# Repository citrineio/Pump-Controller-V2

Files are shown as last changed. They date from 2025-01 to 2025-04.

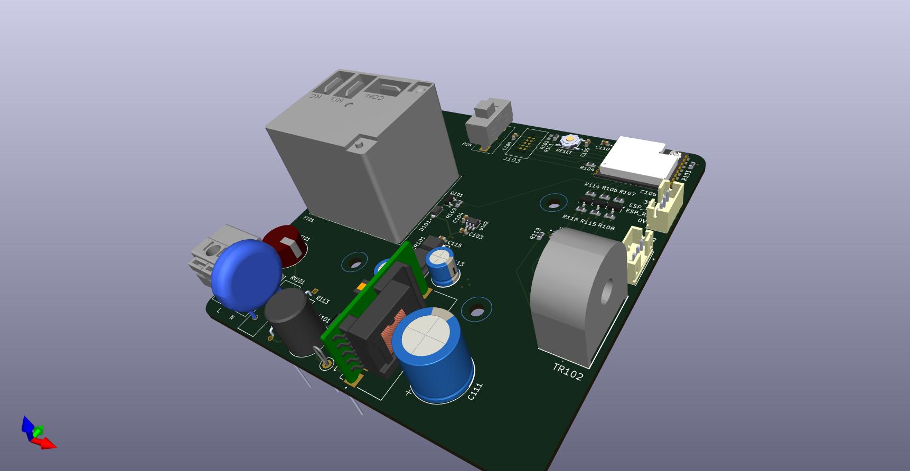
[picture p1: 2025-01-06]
01- Design Files/V4.0/Pump_Controller Side.jpg

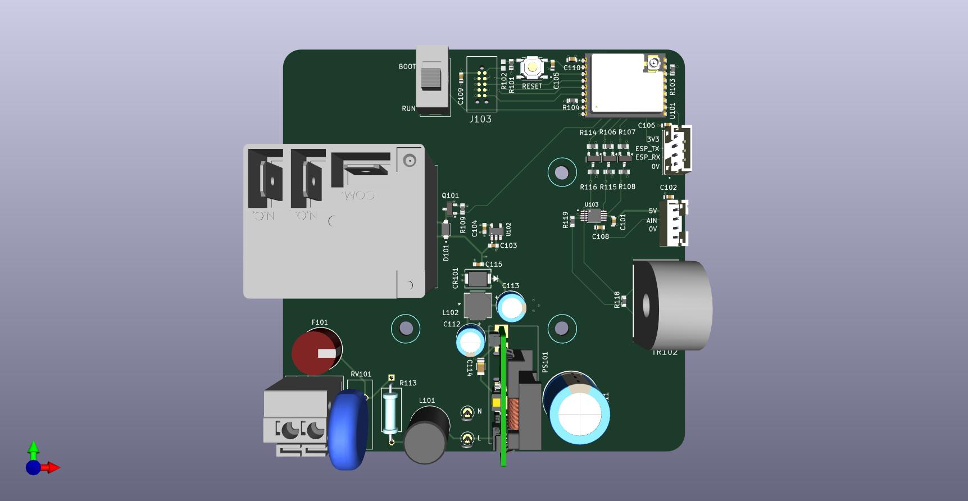
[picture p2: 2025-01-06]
01- Design Files/V4.0/Pump_Controller.jpg

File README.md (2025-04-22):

# Pump Controller

## Description
A device which can monitor and switch household water pumps remotely.
## Constraints
**Power**:  5V wall power adaptor
## Features
- Monitor the on/off status and current consumption
- Switch the pump off if desired.
- Indicate if the pump is running dry. 
- Wireless connectivity
- Matter optional

## Block Diagram

Pump Controller V2

## PCB





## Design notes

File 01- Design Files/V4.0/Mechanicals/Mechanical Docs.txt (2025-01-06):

- Board Outline dxf
- Enclosure STEP File

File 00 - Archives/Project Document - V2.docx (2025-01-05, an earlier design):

# Project Title

# Description

A device which can monitor and switch household water pumps remotely.

# Constraints

Power: Mains voltage 100-240V

Dimensions: Must fit within a typical junction box, preferably a 10x10cm box

# Features

- Monitor the On/Off status and current consumption
- Switch the pump off if desired.
- Indicate if the pump is running dry.
- Wireless connectivity
- Matter optional

# Block Diagram

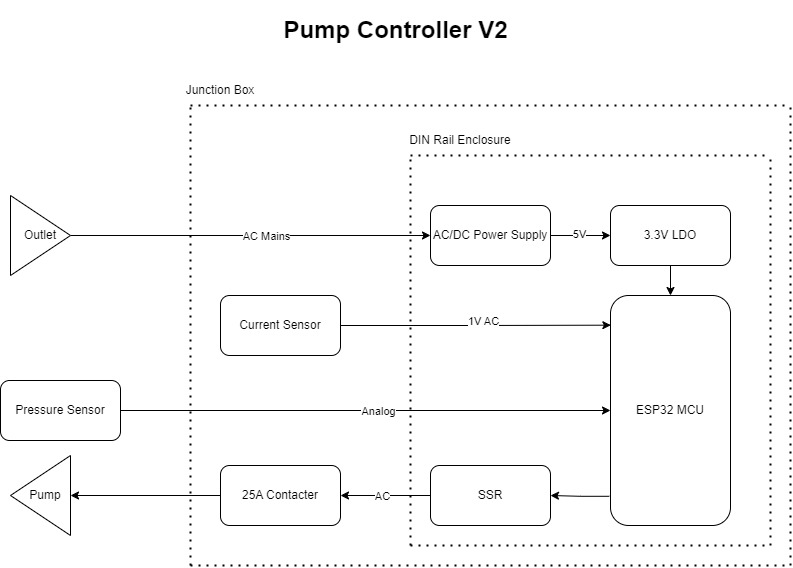
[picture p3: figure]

# Components

MCU: ESP32-C3-MINI-1U-H4

## AC/DC Power Supply: IRM-03-5

## 3.3V LDO: AP2112K-3.3TRG1

## Current Sensor: SCT013-30

Pressure Sensor: Seeed 114991178 or equivalent.

SSR: AQH2223AX

Contactor: Tomzn TOCT1-25 (Aliexpress)

Din Rail Enclosure: Szomk AK-DR-103, LK SHINY LK-DR56 or BUD IND DMB-4771

Box: Minimum 12x12cm

# Power Budget

Component | Voltage/s | Current/s | Power | Type
IRM-03-5 | 5V | 0.6A | 3W | Source
AP2112K-3.3TRG1 | 3.3V | 0.6A | 1.98 | Source
ESP32-C3-MINI-1U-H4 | 3.3V | 0.35A | 1.15W | Sink
114991178 | 5 | 0.01 | 0.05W | Sink
AQH2223AX | 5 | 0.02 | 0.1W | Sink
Total | 1.3W

*Some ICs have multiple voltage rails with different voltage levels.

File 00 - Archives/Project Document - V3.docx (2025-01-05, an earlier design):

# Pump Controller

# Description

A device which can monitor and switch household water pumps remotely.

This version forgoes din rail mounted components including the PCB enclosure and the contactor in favor of a chassis mounted heavy contact relay and a standoff mounted PCB. It also switches to an open frame AC/DC module decreasing the price.

# Constraints

Power: Mains voltage 100-240V

Dimensions: Must fit within a typical junction box, preferably a 10x10cm box

# Features

- Monitor the on/off status and current consumption
- Switch the pump off if desired.
- Indicate if the pump is running dry.
- Wireless connectivity
- Matter optional

# Block Diagram

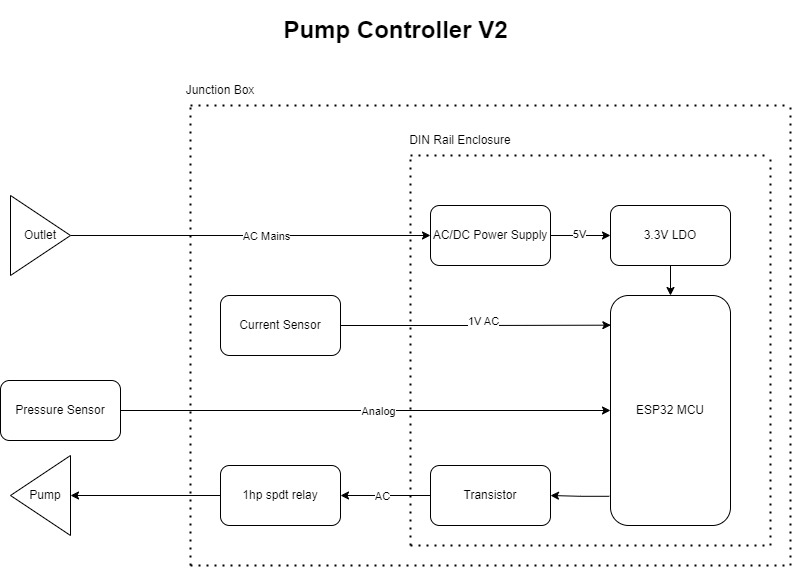
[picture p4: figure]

# Future Improvements

- Utilize 3.81mm or 5.08mm plug-in terminal blocks instead of spring clamp blocks for AC power.
- Utilize 3.81mm plug-in terminal blocks instead of JST connectors.
- Avoid 2.0mm connectors in the future and stick with 2.54mm to enable Dupont cables.
- Replace TC2050 with custom 2x5 2.54mm ISP footprint to utilize testing clamp.
- Replace UART connector with 1x4 2.54mm connector footprint for testing clamp.
- Use Hi-link HLK-PM01 for this application.
- Design a custom enclosure for the PCB and redesign the whole PCB.

# Components

MCU: ESP32-C3-WROOM-02U-N4

## AC/DC Power Supply: PBO-5C-5 2.8$ OR LS05-13B05R3 OR 5ACFEW_05S3

Fuse Holder: 56000001019 or 56000001009

Fuse: 39212000000 or 0034.6618

MOV: B72214S0351K101

Resistor: FMP200JR-52-12R

Input Inductor: RLB9012-472KL

Capacitor: B43821F5226M000

CY: CL31B102KHFNFNE

Output Cap: A750EQ477M1CAAE015

Output inductor: LSXBD6060WHL4R7M

Output Cap 2: ESL107M035AE3AA

TVS: SMBJ7.0CA-13-F

CAP 3: CL10B105KO8NNNC

## 3.3V LDO: AP2112K-3.3TRG1

Zmct102 (pcb mount)

Terminals: WJ142V-5.08-2P

JST Connector: B3B-XH-2(LF)(SN)

Pressure Sensor: Seeed 114991178 or equivalent.

Terminal Block: XY118-5.0-2P

ADC?

Relay: J115F21C5VDCS_9 or az2100-1ce-5def or SLC-5VDC-SL-C

Flyback Diode: 1N4007FL

Transistor: DMG2302U-7

Box: 10x10cm CCTV box

# Power Budget

Component | Voltage/s | Current/s | Power | Type
PBO-5C-5 | 5V | 1A | 5W | Source
AP2112K-3.3TRG1 | 3.3V | 0.6A | 1.98 | Source
ESP32-C3-WROOM-02U-N4 | 3.3V | 0.35A | 1.15W | Sink
114991178 | 5 | 0.01 | 0.05W | Sink
J115F31CH5VDCS61.5U | 5 | 0.3 | 1.5W | Sink
Total | 1.3W

*Some ICs have multiple voltage rails with different voltage levels.

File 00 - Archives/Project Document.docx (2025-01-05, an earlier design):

# Project Title

# Description

A device/product which does X and Y or solves problem Z

# Constraints

Power: Particular power source/ specific battery life

Dimensions: Must fit a specific enclosure

Input/Output Interface:

Specific Components

*These are examples.

# Features

- Can do X
- Connects to Y
- Control Z
- Senses A

# Block Diagram

Having a block diagram is imperative for a quick design process. DRAW.IO is a decent tool.

# Components

MCU/MPU/FPGA/ASIC: Part number of the main IC

Criteria | IC 1 | IC 2
Price | $ | $
Package | QFP/QFN/BGA/SOIC…etc
Manufacturer
Current | Max current consumption/rating
Input Voltage | Min – Max voltage/ nominal voltage
| Mark selected component in green

## Component 1

# Power Budget

Component | Voltage/s | Current/s | Power
Part number 1 | Voltage 1, Voltage 2, Voltage 3… | Current 1, Current 2, Current 3… | Total Power
Part number 2 | Input Voltage | Current Consumption | Power
Part number 3 | Input Voltage | Current Consumption | Power
Total | Total power in Watts

*Some ICs have multiple voltage rails with different voltage levels.

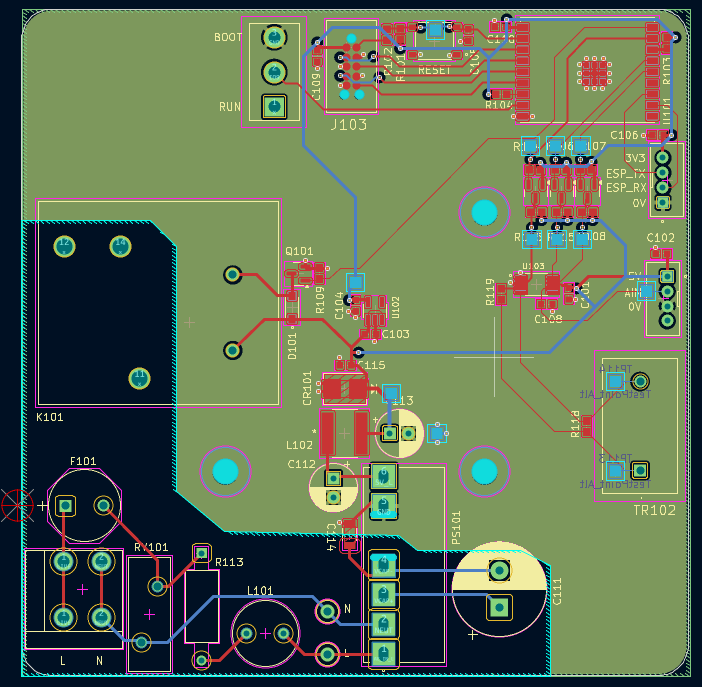
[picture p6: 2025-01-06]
01- Design Files/V4.0/Layout .png

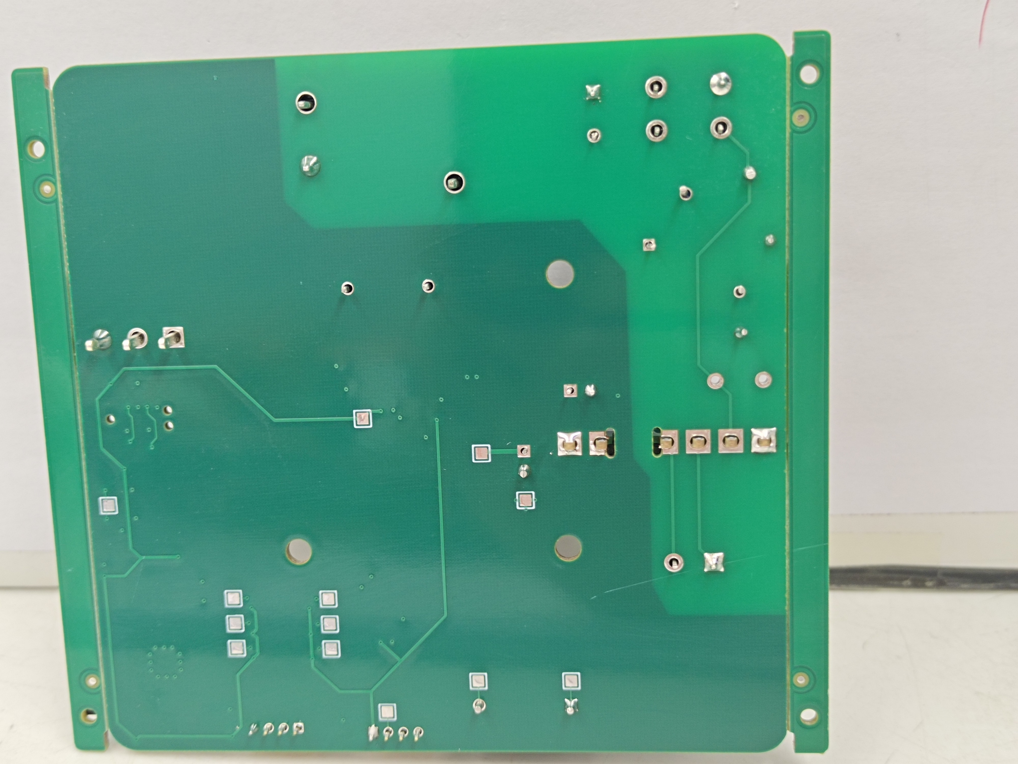
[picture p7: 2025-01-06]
02 - Photos/wKgZomYt3oqAXZ4lACKfuGCoQko008.jpg

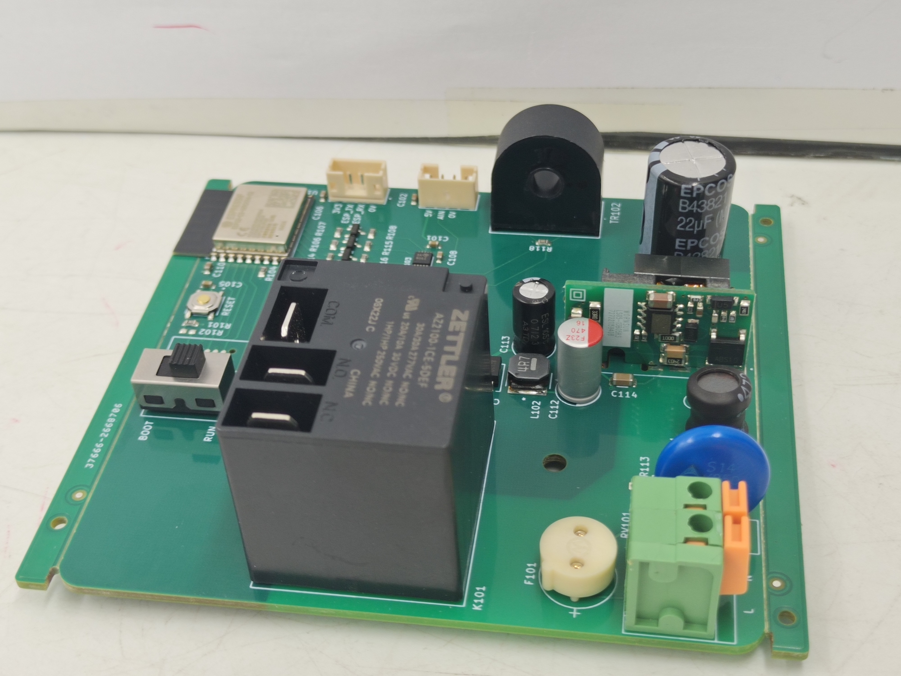
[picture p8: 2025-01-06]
02 - Photos/wKgaomYt3ouAErzlABsgimlviy8659.jpg

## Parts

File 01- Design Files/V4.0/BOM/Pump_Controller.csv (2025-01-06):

Reference | Value | Footprint | Qty | DNP | Manufacturer | Part Number
C101,C102,C103,C104,C106,C108,C109,C110,C111,C112,C113 | 1u | Library:CL10A | 11 |  | Samsung Electro-Mechanics | CL10B105KO8NNNC
C105,C107 | 10u | UltraLibrarian:CAP_CL21_SAM | 2 |  | Samsung Electro-Mechanics | CL21A106KAYNNNE
D101,D103 | 1N5819HW-7-F | Diode_SMD:D_SOD-123 | 2 |  | Diodes Incorporated | 1N5819HW-7-F
D102 | GRN | LED_SMD:LED_0603_1608Metric | 1 |  | Everlight Elec | 19-217/GHC-YR1S2/3T
F101 | SRF1206P150 | Library:PTC_1206_3216Metric | 1 |  | prosemi | SRF1206P150
J101,J106,J107 | Screw_Terminal_01x02 | Samacsys:DG30825402P1400AH | 3 |  | DEGSON | DG308-2.54-02P-14-00A(H)
J102 | Conn_01x04 | Connector_PinHeader_2.54mm:PinHeader_1x04_P2.54mm_Vertical | 1
J104 | Conn_02x05_Odd_Even | Connector_PinHeader_2.54mm:PinHeader_2x05_P2.54mm_Vertical | 1
J105 | Screw_Terminal_01x03 | Samacsys:DG30825403P1400AH | 1 |  | DEGSON | DG308-2.54-03P-14-00A(H)
K101 | AZ2100-1CE-5DEF | Library:AZ2100-1CE-5DEF | 1 |  | American Zettler | AZ2100-1CE-5DEF
Q101,Q103 | C20917 | Package_TO_SOT_SMD:SOT-23 | 2 |  | Alpha & Omega Semicon | AO3400A
R101,R102,R103,R107,R108,R110,R111,R115 | 10K | Library:RESC1607X60N | 8 |  | UNI-ROYAL(Uniroyal Elec) | 0603WAF1002T5E
R104,R105,R113 | 2k2 | Library:RESC1607X60N | 3 |  | UNI-ROYAL(Uniroyal Elec) | 0603WAF2201T5E
R109 | 68R | Library:RESC1607X60N | 1 |  | UNI-ROYAL(Uniroyal Elec) | 0603WAF680JT5E
TR101 | ZMCT102 | Library:zmct102 | 1 |  | Qingxian Zeming Langxi Electronic | ZMCT102
U101 | AP2112K-3.3 | Library:SOT95P285X140-5N | 1 |  | Diodes Incorporated | AP2112K-3.3TRG1
U102 | ESP32-C3-WROOM | Library:MODULE_ESP32-C3-WROOM-02-H4 | 1 |  | Espressif Systems | ESP32-C3-WROOM-02-N4
U103 | TXS0104EPWR | Snapeda:TXS0104EPWR_SOP65P640X120-14N | 1
U104 | ADS1115IDGSR | Library:ADS1115_SOP50P490X110-10N | 1 |  | Texas Instruments | ADS1115IDGSR

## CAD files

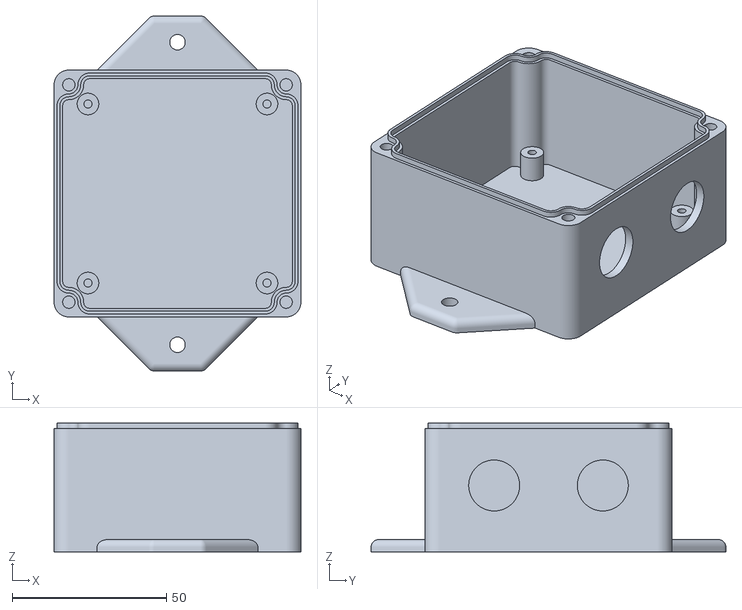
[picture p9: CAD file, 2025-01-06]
01- Design Files/V4.0/Mechanicals/Enclosure/C-1Y6W328612A_box_V6.1.stl
80.0 x 115.0 x 41.7

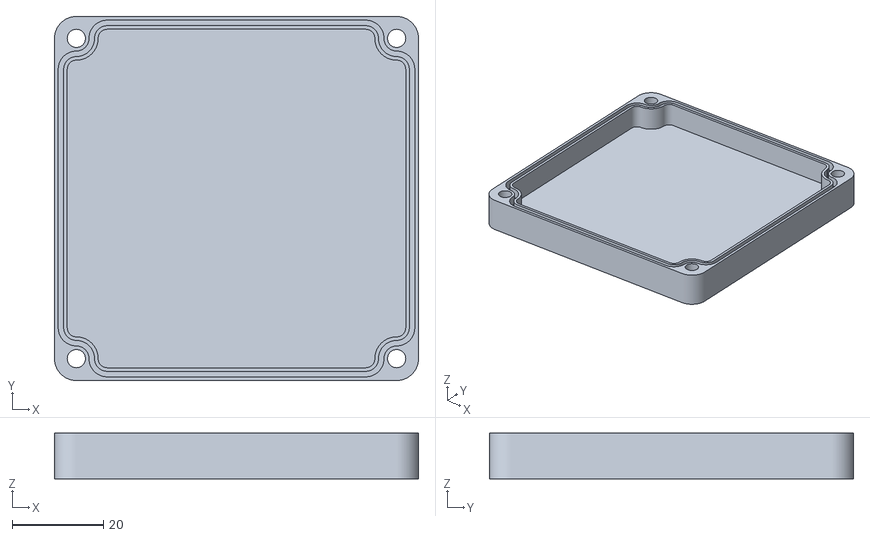
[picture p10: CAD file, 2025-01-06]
01- Design Files/V4.0/Mechanicals/Enclosure/C-1Y5W328612A_lid.stl
80.0 x 80.0 x 10.00

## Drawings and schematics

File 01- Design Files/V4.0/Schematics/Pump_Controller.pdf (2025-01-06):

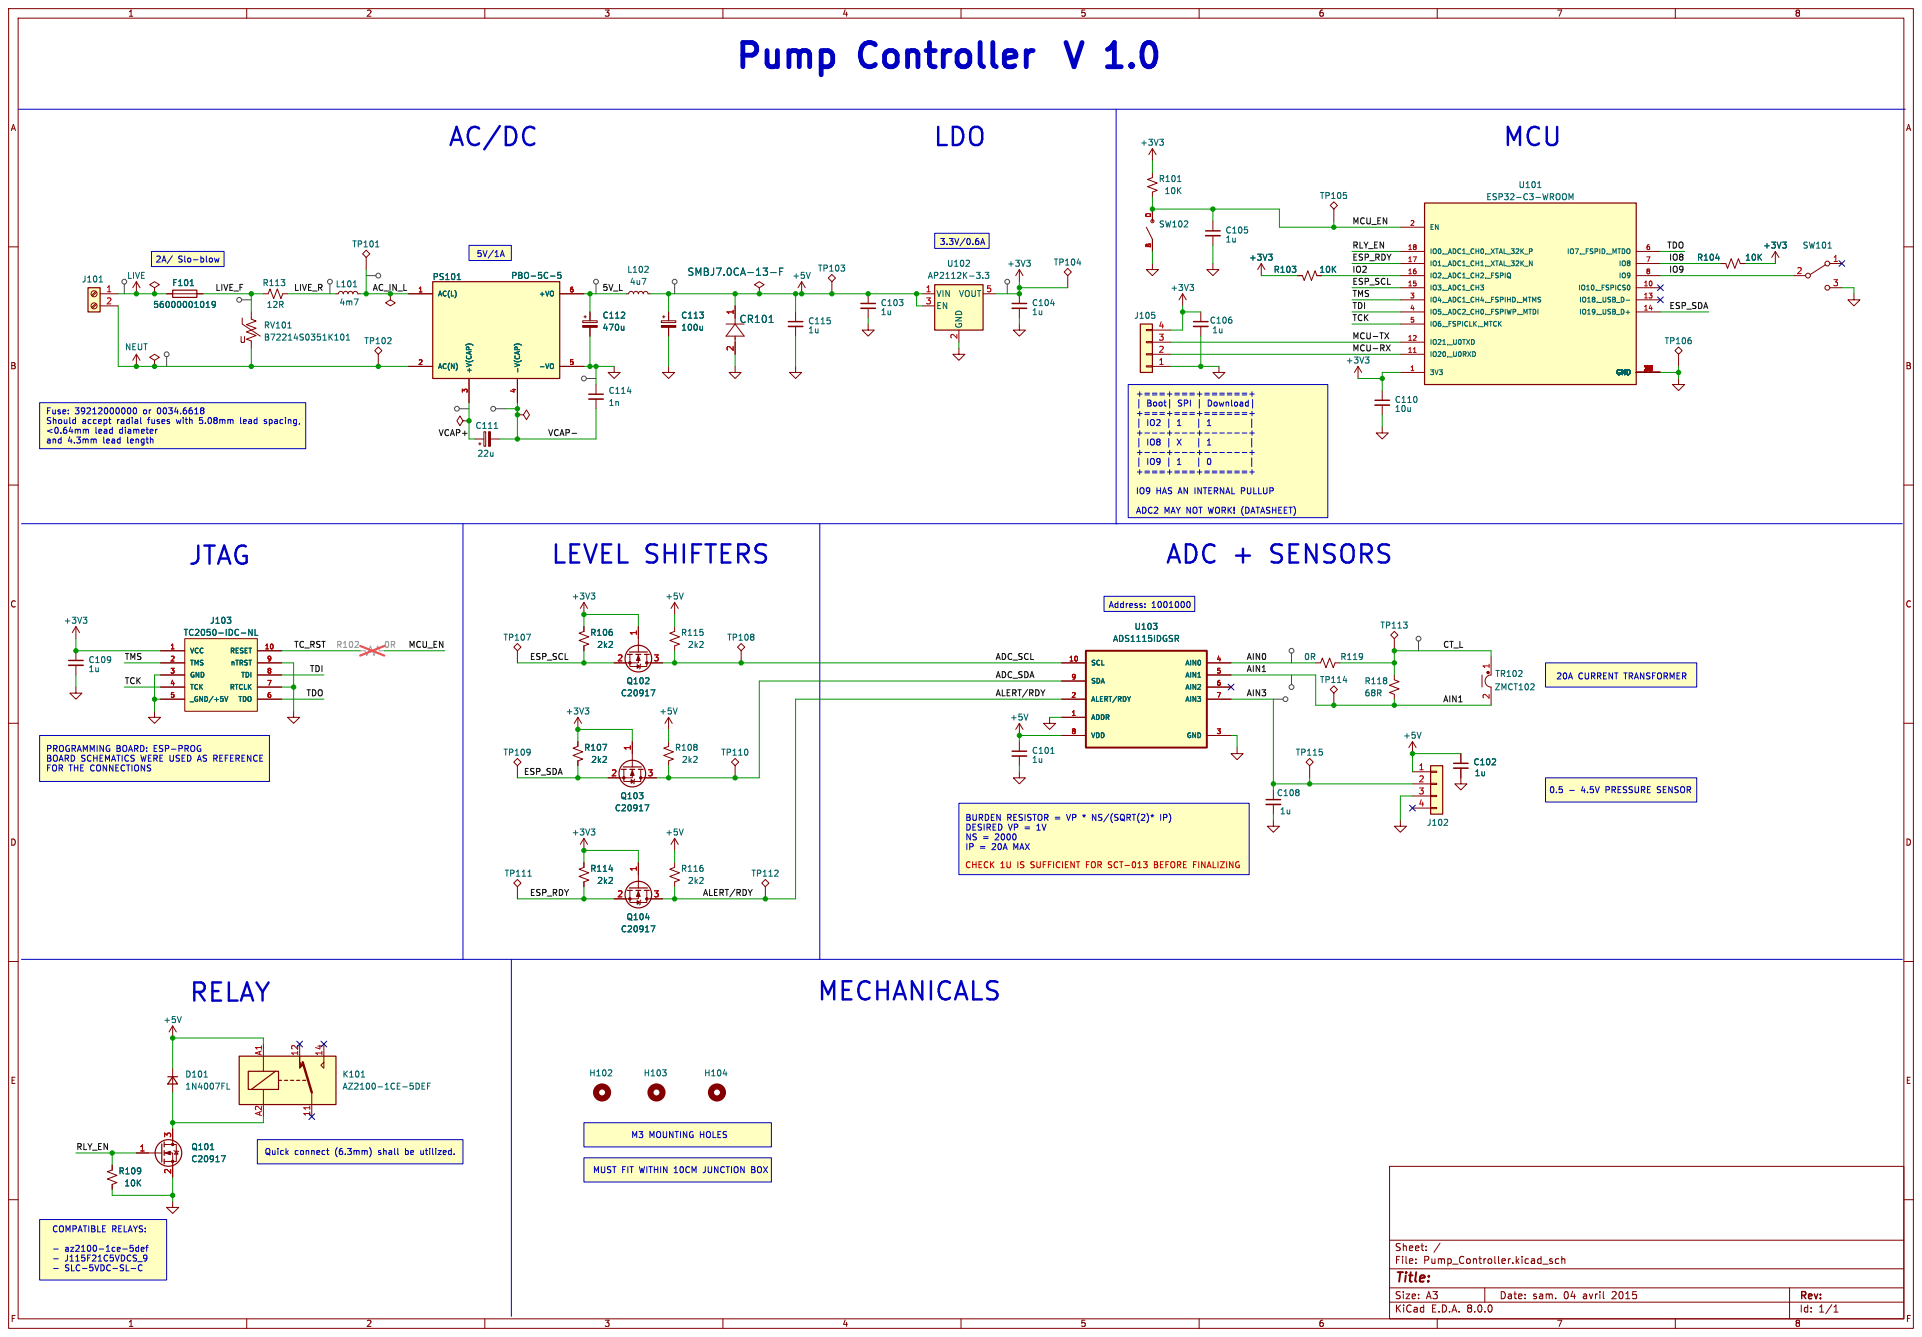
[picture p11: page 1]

IP = 20A MAX Pump Controller

IO9 HAS AN INTERNAL PULLUP
ADC + SENSORS

ADC2 MAY NOT WORK! (DATASHEET) M3 MOUNTING HOLES

PROGRAMMING BOARD: ESP-PROG
BOARD SCHEMATICS WERE USED AS REFERENCE

MUST FIT WITHIN 10CM JUNCTION BOX

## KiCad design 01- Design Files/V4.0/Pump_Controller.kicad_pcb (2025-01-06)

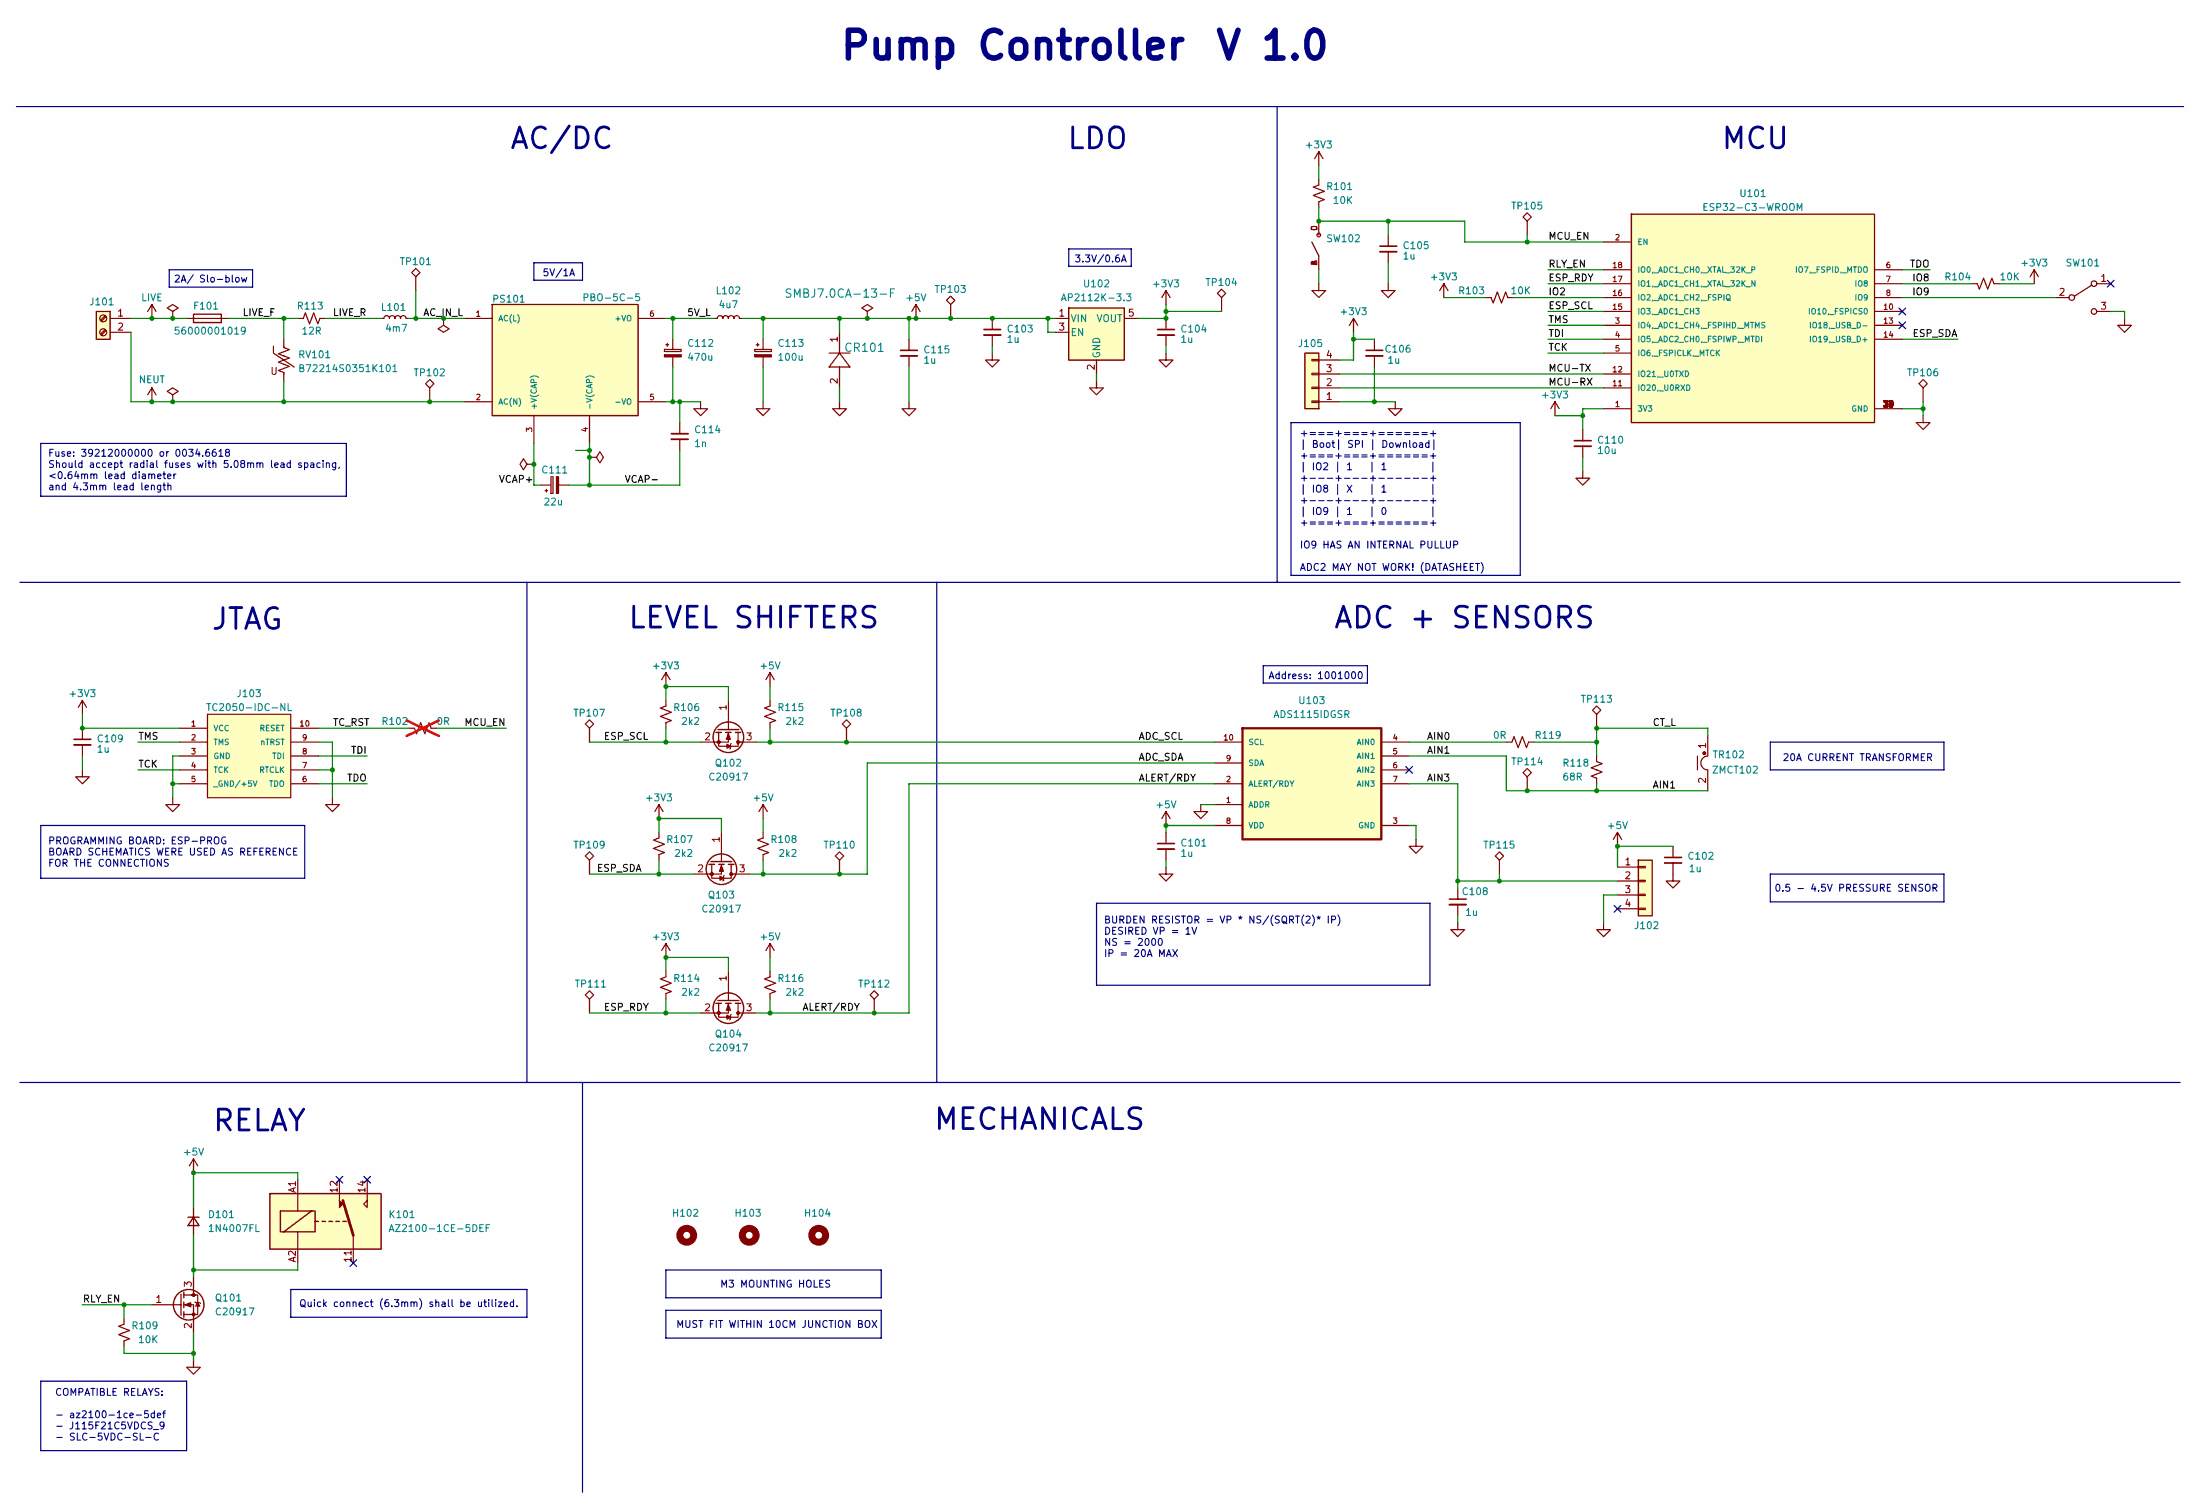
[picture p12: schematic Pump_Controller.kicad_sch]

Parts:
C101, C102, C103, C104, C105, C106, C108, C109, C115: 1u; CL10A; Part Number CL10B105KO8NNNC - C59782
C110: 10u; CL10A; Part Number CL10A106MA8NRNC - C96446
C111: 22u; CP_Radial_D12.5mm_P5.00mm; Part Number B43821F5226M000
C112: 470u; CP_Radial_D6.3mm_P2.50mm; Part Number A750EQ477M1CAAE015
C113: 100u; CP_Radial_D6.3mm_P2.50mm; Part Number ESL107M035AE3AA
C114: 1n; CAP_CL31_SAM; Part Number CL31B102KHFNFNE
CR101: SMBJ7.0CA-13-F; SMB_DIO; Part Number SMBJ7.0CA-13-F
D101: 1N4007FL; SODFL3618X110N; Part Number 1N4007FL
F101: 56000001019; FUSE_560_1019_LTF; Part Number 56000001019
H102, H103, H104: MountingHole; MountingHole_3.2mm_M3
J101: Screw_Terminal_01x02; CONN-TH_2P-P5.08_WJ142V-5.08-2P
J102, J105: B4B-PH-K; JST_B4B-PH-K; Part Number B4B-PH-K
J103: TC2050-IDC-NL; TAG-CONNECT_TC2050-IDC-NL
K101: AZ2100-1CE-5DEF; Part Number AZ2100-1CE-5DEF
L101: 4m7; IND_RLB9012-472KL; Part Number RLB9012-472KL
L102: 4u7; IND_HL4R7M_TAY; Part Number LSXBD6060WHL4R7M
PS101: PBO-5C-5; CONV_PBO-5C-5; Part Number PBO-5C-5
Q101, Q102, Q103, Q104: C20917; SOT-23; Part Number AO3400A
R101, R103, R104, R109: 10K; RESC1607X60N; Part Number 0603WAF1002T5E - C25804
R102: 0R; RESC1607X60N; Part Number 0603WAF0000T5E - C21189; not fitted
R106, R107, R108, R114, R115, R116: 2k2; RESC1607X60N; Part Number 0603WAF2201T5E- C4190
R113: 12R; YAG_FMP200_YAG; Part Number FMP200JR-52-12R
R118: 68R; RESC1607X60N; Part Number 0603WAF680JT5E- C27592
R119: 0R; RESC1607X60N; Part Number 0603WAF0000T5E - C21189
RV101: B72214S0351K101; VAR_B72214S0351K101; Part Number B72214S0351K101
SW101: SW_SPDT; SS12D10L3; Part Number SS-12D10L3
SW102: TS-1187A-B-A-B; SW_TS-1187A-B-A-B; Part Number TS-1187A-B-A-B
TP101, TP102: TestPoint_Alt; TestPoint_Loop_D2.50mm_Drill1.0mm
TP103, TP104, TP105, TP106, TP107, TP108, TP109, TP110, TP111, TP112, TP113, TP114, TP115: TestPoint_Alt; TestPoint_Pad_1.5x1.5mm
TR102: ZMCT102; zmct102; Part Number ZMCT102
U101: ESP32-C3-WROOM; XCVR_ESP32-C3-WROOM-02U-N4; Part Number ESP32-C3-WROOM-02-N4
U102: AP2112K-3.3; SOT95P285X140-5N; Part Number AP2112K-3.3
U103: ADS1115IDGSR; ADS1115_SOP50P490X110-10N; Part Number ADS1115IDGSR

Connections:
+3V3: C104.1, C106.1, C109.1, C110.1, J103.1 (VCC), J105.4, Q102.1 (G), Q103.1 (G), Q104.1 (G), R101.1, R103.1, R104.2, R106.1, R107.1, R114.1, TP104.1, U101.1 (3V3), U102.5 (VOUT)
+5V: C101.1, C102.1, C103.1, C113.1, C115.1, CR101.1, D101.1 (K), J102.1, K101.A1, L102.2, R108.1, R115.1, R116.1, TP103.1, U102.1 (VIN), U102.3 (EN), U103.8 (VDD)
/5V_L: C112.1, L102.1, PS101.6 (+VO)
/AC_IN_L: L101.2, PS101.1 (AC(L)), TP101.1
/ADC_SCL: Q102.3 (D), R115.2, TP108.1, U103.10 (SCL)
/ADC_SDA: Q103.3 (D), R108.2, TP110.1, U103.9 (SDA)
/AIN0: R119.2, U103.4 (AIN0)
/AIN1: R118.2, TP114.1, TR102.2, U103.5 (AIN1)
/AIN3: C108.1, J102.2, TP115.1, U103.7 (AIN3)
/ALERT/RDY: Q104.3 (D), R116.2, TP112.1, U103.2 (ALERT/RDY)
/CT_L: R118.1, R119.1, TP113.1, TR102.1
/ESP_RDY: Q104.2 (S), R114.2, TP111.1, U101.17 (IO1,_ADC1_CH1,_XTAL_32K_N)
/ESP_SCL: Q102.2 (S), R106.2, TP107.1, U101.15 (IO3,_ADC1_CH3)
/ESP_SDA: Q103.2 (S), R107.2, TP109.1, U101.14 (IO19,_USB_D+)
/IO2: R103.2, U101.16 (IO2,_ADC1_CH2,_FSPIQ)
/IO8: R104.1, U101.7 (IO8)
/IO9: SW101.2 (B), U101.8 (IO9)
/LIVE_F: F101.2, R113.1, RV101.1
/LIVE_R: L101.1, R113.2
/MCU-RX: J105.2, U101.11 (IO20,_U0RXD)
/MCU-TX: J105.3, U101.12 (IO21,_U0TXD)
/MCU_EN: C105.1, R101.2, R102.2, SW102.C, SW102.D, TP105.1, U101.2 (EN)
/RLY_EN: Q101.1 (G), R109.1, U101.18 (IO0,_ADC1_CH0,_XTAL_32K_P)
/TCK: J103.4 (TCK), U101.5 (IO6,_FSPICLK,_MTCK)
/TC_RST: J103.10 (RESET), R102.1
/TDI: J103.8 (TDI), U101.4 (IO5,_ADC2_CH0,_FSPIWP,_MTDI)
/TDO: J103.6 (TDO), U101.6 (IO7,_FSPID,_MTDO)
/TMS: J103.2 (TMS), U101.3 (IO4,_ADC1_CH4,_FSPIHD,_MTMS)
/VCAP+: C111.1, PS101.3 (+V(CAP))
/VCAP-: C111.2, C114.2, PS101.4 (-V(CAP))
GND: C101.2, C102.2, C103.2, C104.2, C105.2, C106.2, C108.2, C109.2, C110.2, C112.2, C113.2, C114.1, C115.2, CR101.2, J102.3, J103.3 (GND), J103.5 (_GND/+5V), J103.7 (RTCLK), J103.9 (nTRST), J105.1, PS101.5 (-VO), Q101.2 (S), R109.2, SW101.3 (C), SW102.A, SW102.B, TP106.1, U101.9 (GND), U101.19 (GND), U101.20 (GND), U101.21 (GND), U101.22 (GND), U101.23 (GND), U101.24 (GND), U101.25 (GND), U101.26 (GND), U101.27 (GND), U101.28 (GND), U101.29 (GND), U101.30 (GND), U101.31 (GND), U101.32 (GND), U101.33 (GND), U101.34 (GND), U101.35 (GND), U101.36 (GND), U101.37 (GND), U101.38 (GND), U101.39 (GND), U102.2 (GND), U103.1 (ADDR), U103.3 (GND)
LIVE: F101.1, J101.1
NEUT: J101.2, PS101.2 (AC(N)), RV101.2, TP102.1
unnamed: D101.2 (A), K101.A2, Q101.3 (D)

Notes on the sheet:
+===+===+======+ | Boot| SPI | Download| +===+===+======+ | IO2 | 1 | 1 | +---+---+------+ | IO8 | X | 1 | +---+---+------+ | IO9 | 1 | 0 | +===+===+======+ IO9 HAS AN INTERNAL PULLUP ADC2 MAY NOT WORK! (DATASHEET)
5V/1A
0.5 - 4.5V PRESSURE SENSOR
LEVEL SHIFTERS
Quick connect (6.3mm) shall be utilized.
3.3V/0.6A
AC/DC
MUST FIT WITHIN 10CM JUNCTION BOX
RELAY
COMPATIBLE RELAYS: - az2100-1ce-5def - J115F21C5VDCS_9 - SLC-5VDC-SL-C
BURDEN RESISTOR = VP * NS/(SQRT(2)* IP) DESIRED VP = 1V NS = 2000 IP = 20A MAX
PROGRAMMING BOARD: ESP-PROG BOARD SCHEMATICS WERE USED AS REFERENCE FOR THE CONNECTIONS
JTAG
M3 MOUNTING HOLES
20A CURRENT TRANSFORMER
Pump Controller
LDO
Fuse: 39212000000 or 0034.6618 Should accept radial fuses with 5.08mm lead spacing, <0.64mm lead diameter and 4.3mm lead length
Address: 1001000
MECHANICALS
2A/ Slo-blow
MCU
ADC + SENSORS
V 1.0

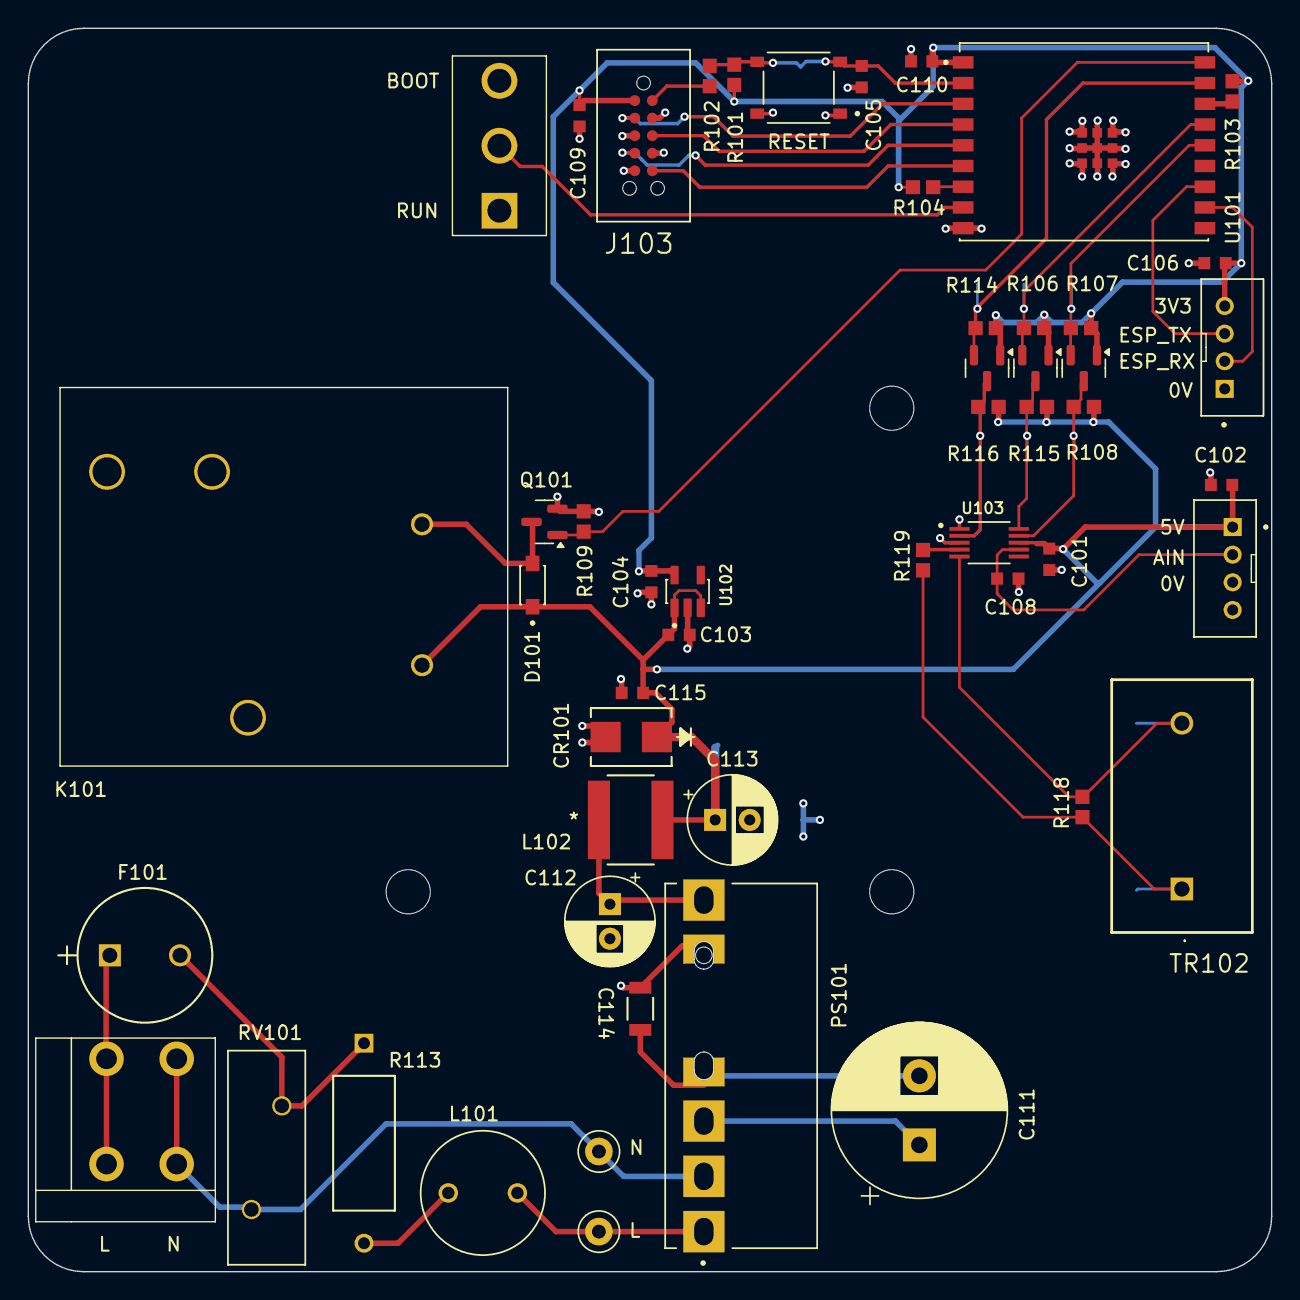
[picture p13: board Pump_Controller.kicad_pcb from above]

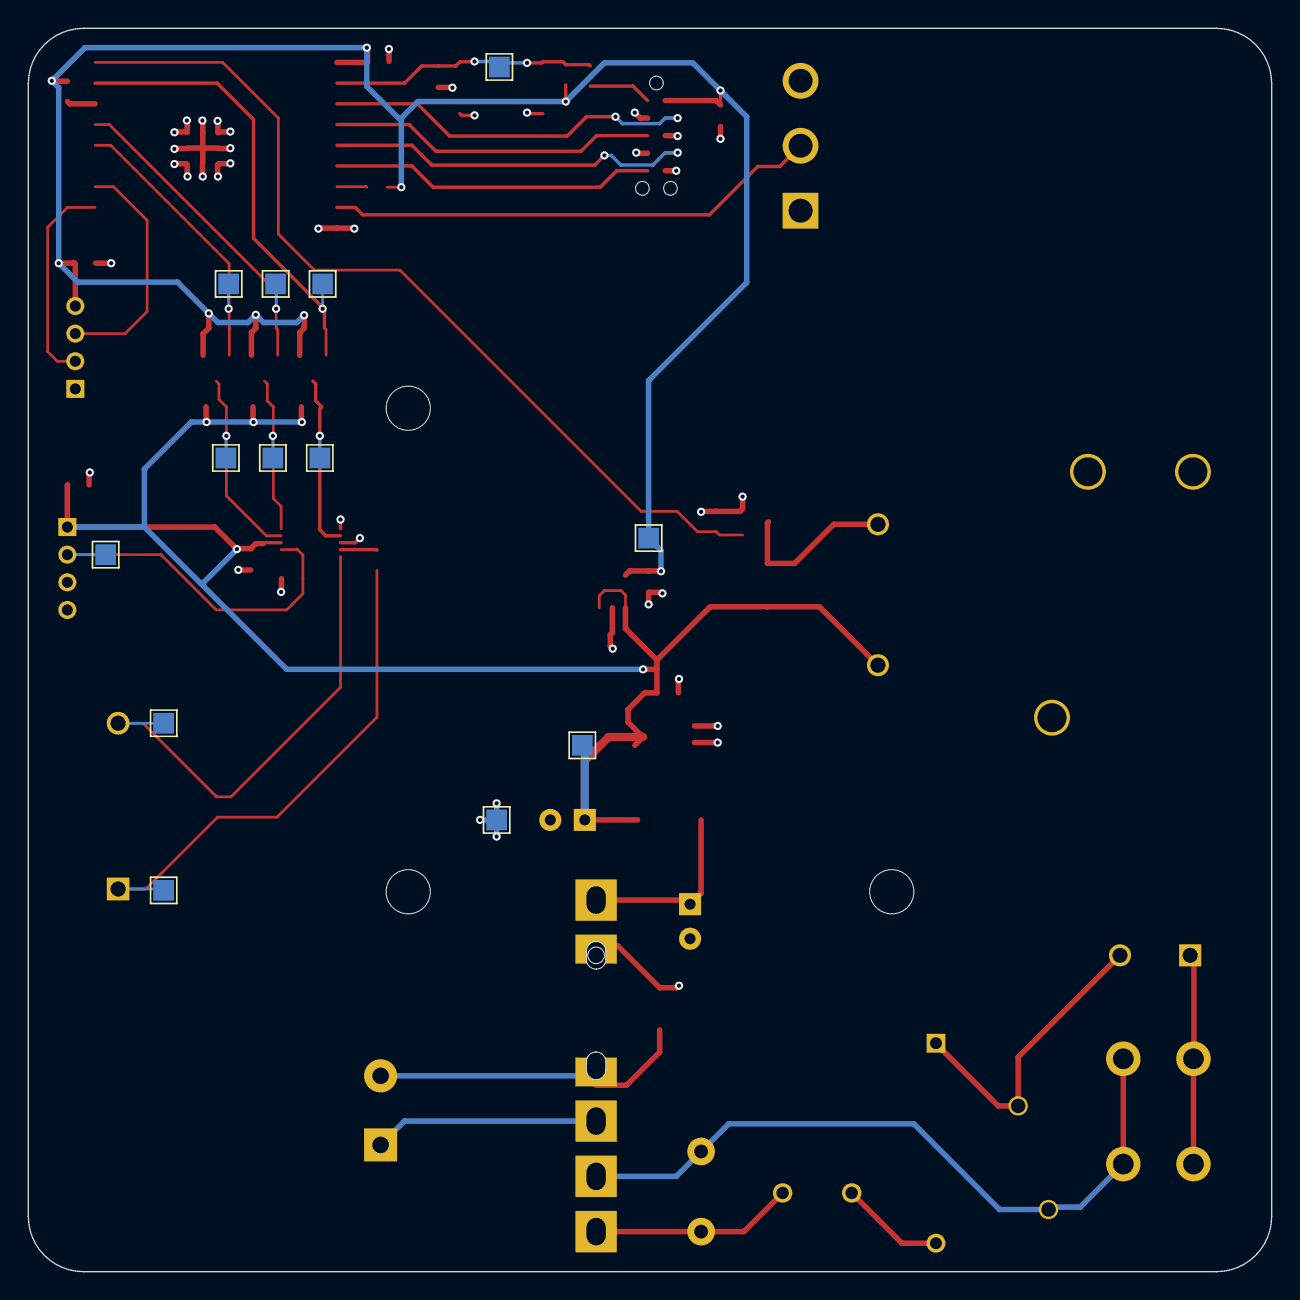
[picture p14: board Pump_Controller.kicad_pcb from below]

Board: 4 copper layers, 90.0 x 90.0 mm, 68 parts (13 on the bottom side), 34 nets.

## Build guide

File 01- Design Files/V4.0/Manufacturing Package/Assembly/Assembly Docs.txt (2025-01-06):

- Component Positions File (Pick and Place/Centroid)
- Assembly Drawing
- 3D PCB Model file (STEP)

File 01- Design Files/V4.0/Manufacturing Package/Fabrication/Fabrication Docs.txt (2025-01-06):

- Silk Screen (Legend)
- Solder Paste
- Solder Mask
- Copper Layers
- Outline
- Drills (PTH and NPTH)
- Drills Map
- Fabrication Drawing in PDF(Board, dimensions, stackup, fab notes)
